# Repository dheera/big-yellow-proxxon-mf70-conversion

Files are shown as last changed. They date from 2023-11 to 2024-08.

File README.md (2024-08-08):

# Big Yellow Proxxon MF70 CNC conversion

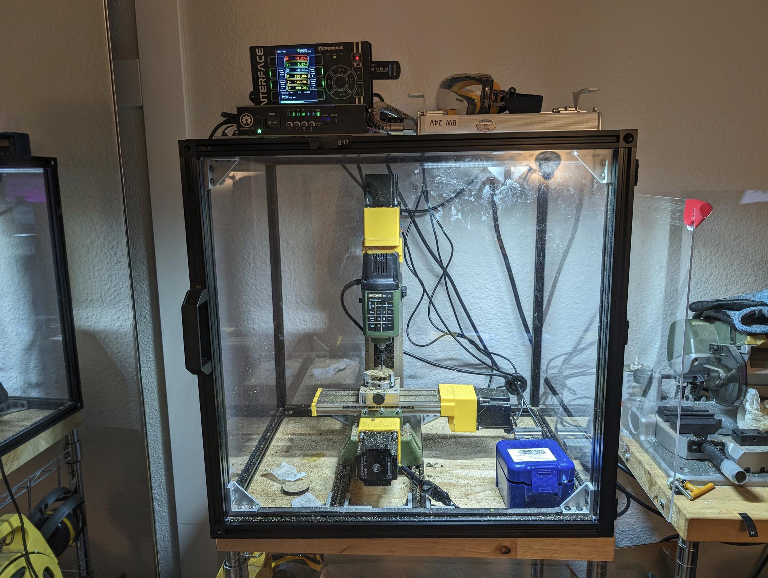
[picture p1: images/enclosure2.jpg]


This repo is a Proxxon MF70 mill CNC conversion based on 3D printed and off-the-shelf mechanical parts, with **Y axis extended from 46mm to 90mm** and **Z axis extended by 15mm**.

I also included a couple parts for if you just want to extend the Y axis for hand milling only, but CNC is the main point of this repo.

I'm lazy to create a name for it, but in the spirit of the [Bubblegum](https://www.youtube.com/playlist?list=PLYxf6JVpXtyO_PyjGGxkbttEl6JiWM5uO) conversion I printed all the parts in yellow so I'm just calling it that.

### What is a Proxxon MF70?

If you are here you probably already have one, but the [Proxxon MF70](https://www.proxxon.com/us/micromot/37110.php) is a cheap, tiny 3-axis mill that sells for around USD 400, sometimes as cheap as 200-300 on Craigslist or eBay and is been a popular target of CNC conversions by hobbyists living in small spaces. The full machine with CNC conversion and enclosure is no larger than a typical 3D printer.

This mill has a number of limitations, but perhaps the biggest of which is that the Y axis is only limited to 46mm of travel. It is fairly straightforward to extend this Y axis to 90mm. The Z axis is also limiting as it only has 70mm of travel, starts from uselessly low, which makes it hard to use a 4th ("A" or rotational) axis. **Both of these limitations are addressed in this conversion.**

There are other limitations with this cheap mill but not addressed here. (Anti-backlash nuts, brushless motor upgrade, new spindle, ACME screws, ball screws, etc. -- but you can still do these things on top of this conversion if you wish.)

If you have a 3D printer to print the parts in this repo, and want a mini **CNC mill for $500-$600 total**, this is it. If you want to spend $1200 or more, there are better options available.

### Why another MF70 conversion?

I wasn't fully happy with any of the existing conversions.

The AliExpress conversion kits are cheap but don't address Y axis or Z axis limitations, use self-tapping screws to hold the entire weight of stepper motors which I am not confident about, and use only 2 out of the 4 mounting screws to hold NEMA23 motors, which is not good for stability. I do, however, like their couplers that attach to the existing handles of the MF70 and use those couplers in this conversion.

The Robotpark conversion has the same issues as the AliExpress kit at a 5X-10X markup, and judging from pictures, seems to just use the same parts as the AliExpress kits.

Proxxon's own CNC-ready MF70 allows a greater Y axis travel of 70mm, which is better than the 46mm, but I am achieving 90mm here. It also does not address the Z axis height at all.

The [Bubblegum](https://www.youtube.com/playlist?list=PLYxf6JVpXtyO_PyjGGxkbttEl6JiWM5uO) conversion is a nicely designed kit but addresses neither Y nor Z axis limitations. I take a couple inspirations from it.

[This](http://www.jarkman.co.uk/catalog/cnc/mf70.htm) conversion involves taking off the knobs fully and purchasing additional shaft couplers, which I also didn't want to do, though if you'd like to do that, you can still use the mounting parts in this repo, and might just need to adjust the M5 spacer lengths.

[This](https://www.thingiverse.com/thing:4375769) conversion is a lot of work and addresses backlash but does not solve the Y or Z axis limitations.

There are a number of other complicated DIY conversions out there that do address the Y and Z axis limitations, but I wasn't happy with any of their designs or complexity. Some involve 5 billion parts, some involve machining metal parts (which is great *after* you have a CNC mill but not before), [some people](https://www.youtube.com/watch?v=0PCznyqI1Co) have effectively replaced the entire machine, which is impressive and I have a lot of respect for, but it is too much for me (If I wanted to do that I might as well build the machine from scratch).

I wanted this to extend the Y and Z axis and stick to 3D printed parts and off-the-shelf parts while keeping the cost of conversion well under the cost of the mill itself.

## Tools
* 3D printer and PETG, ABS, nylon, or other strong and chemically-resistant filament (do not use PLA!)
* Drill press
* Normal 3mm drill bit
* Extra long (120mm long) 3mm drill bit
* 90-degree countersink bit
* Dremel with cutting disc, or other tool that can cut threaded rods
* Blue Loctite

## Off-the-shelf parts

I include McMaster links for all the parts below for convenience, if you want to order them all in one go, and to serve as permalinks for what the exact part should look like. However, McMaster is expensive. If you want to save money you can find equivalent parts for almost everything on Amazon or eBay, though since the suppliers are constantly changing, there is no way to permalink to those sites. I have included Amazon search result links below, so verify that they match the specified dimensions before purchasing.

* 4 x M3 threaded rod, 2 cut to ? for X axis and 2 cut to ? for Y axis [McMaster](https://www.mcmaster.com/90024A218/) | [Amazon](https://www.amazon.com/s?k=m3+threaded+rod+300mm)
* 6 x M3 square nut, 5.5mm x 5.5mm x 1.8mm [McMaster](https://www.mcmaster.com/97258A101/) | [Amazon](https://www.amazon.com/s?k=m3+square+nut+1.8mm)
* 6 x ID=6 OD=12 L=4.5 thrust ball bearings [McMaster](https://www.mcmaster.com/7806K58/) | [Amazon](https://www.amazon.com/s?k=6x12x4.5+ball+bearing)
* 1 x ID=6 OD=13 L=5 steel spacer [McMaster](https://www.mcmaster.com/92871A241/) 
* 1 x ID=6 OD=13 L=2 steel spacer [McMaster](https://www.mcmaster.com/92871A198/)
* 8 x ID=5 OD=10 L=35 aluminum spacer [McMaster](https://www.mcmaster.com/94669A148/)
* 4 x ID=5 OD=10 L=45 aluminum spacer [McMaster](https://www.mcmaster.com/94669A152/)
* 4 x M5 L=50 flat head countersunk screws [McMaster](https://www.mcmaster.com/92125A228/)
* 4 x M5 L=65 flat head countersunk screws [McMaster](https://www.mcmaster.com/92125A230/)
* 4 x M5 L=75 flat head countersunk screws [McMaster](https://www.mcmaster.com/92125A109/) -- if you want to save money you can also just get a box of L=75 and skip the L=50 and L=65 above, but you'll have a hell of a time tightening lock nuts over the extra length
* 4 x M3 L=50 hex bolt socket cap screws
* AliExpress MF70 NEMA23 conversion shaft couplers -- you only need the "round parts" from the conversion kit -- there are some sellers which will sell only those parts to you [AliExpress](https://www.aliexpress.us/w/wholesale-mf70-nema23.html?spm=a2g0o.productlist.search.0)
* 3 x good quality NEMA23 motors with 5mm mounting holes (some have 4mm holes, but this kit is designed for 5mm) [OpenBuilds](https://openbuildspartstore.com/nema-23-stepper-motor/) | [StepperOnline](https://www.omc-stepperonline.com/p-series-nema-23-bipolar-1-8deg-1-26nm-178-4oz-in-2-8a-2-5v-57x57x56mm-4-wires-23hp22-2804s) 

### 3D printed parts

For the CNC conversion, print all the parts starting with **all-** and **cnc-** in the **stl/** directory.

If you just want a hand mill with Y axis extension, print everything starting with **all-** and **hand-** and ignore the CNC parts. You also only need a fraction of the off-the-shelf parts above, I'm sure you can figure it out.

I recommend printing everything at 100% infill with PETG, ABS, nylon, or other good material. I highly recommend you do not use PLA. Don't skimp on the infill, this is a mill, and if you're using PETG it will cost you a whopping $9 to print all these parts at 100%.

I recommend printing parts with large surface area (all-y-channel, cnc-x-rightplate, cnc-y-frontplate, cnc-z-topplate) with a brim to avoid lifting and warping at the corners, as the **flatness of the bottom surface is crucial** on many parts. If you don't have lifting/warping problems you can ignore this. Besides using a brim, for PETG, 2 things help to avoid warping: (a) use a higher bed temp like 90 C (b) use an enclosure or put your 3D printer in a closet so the ambient temperature rises to around 30 C - 40 C.

### Extra hardware

## Instructions

### Take apart the X and Y axes

Remove the 2 axis stage, take apart the Y axis (noting that the lead screw is left-threaded), and then take apart the X axis (right-threaded) until you are down to this. Note that the "Proxxon" logo is on the front side, but we will take that off later, so you may want to mark the front side of the aluminum plate with a grease pen or scribe. Note that Proxxon's X and Y axis aluminum plates are intentionally NOT perfectly symmetrical by design, so when you put them back together the direction matters or you will not be able to assemble it.

Drop in the 3D printed "all-y-channel". It should fit snugly. Note that the channel is not symmetrical and there is a correct front and back side. You may want to mark the front end of this as well for convenience. You may have to slightly loosen the screws slightly to drop the channel in. Don't take them off fully yet, to ensure the holes you drill in the next step are properly aligned.

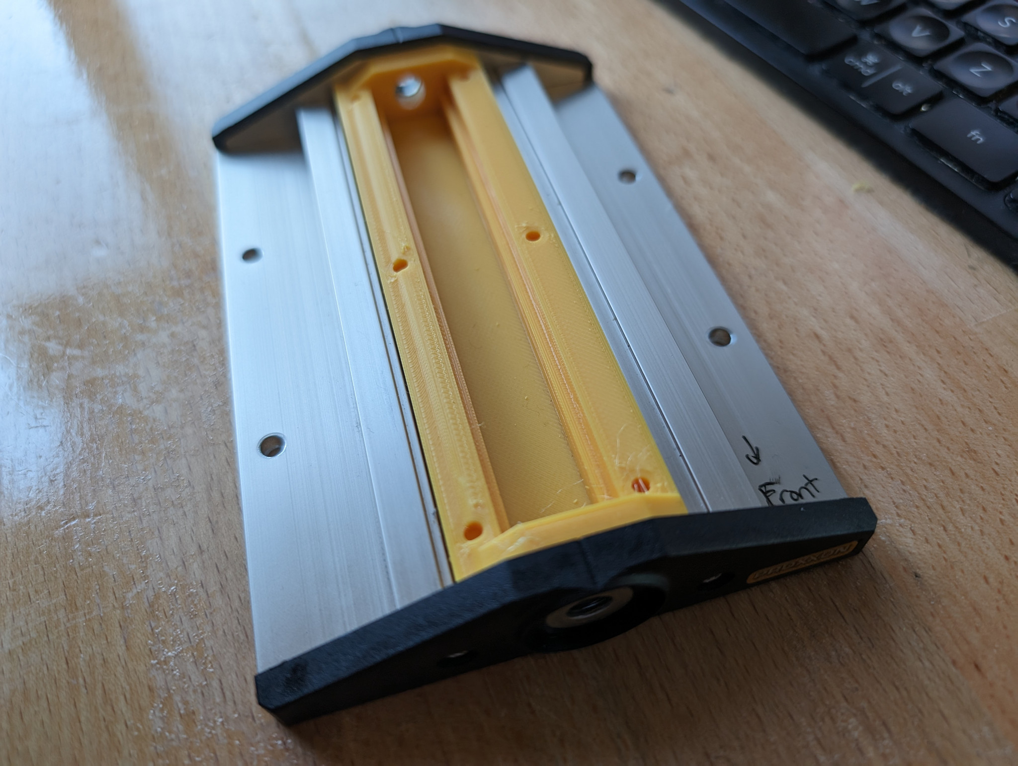
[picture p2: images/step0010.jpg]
step0010


### Modify the Y axis plate

With a drill press and regular 3mm drill bit, drill out the 6 marked holes in the 3D printed channel all the way down and drill fully through the aluminum plate below. You can also, if you prefer, just barely touch the aluminum to mark the center, remove the channel, and then drill out the aluminum, to avoid aluminum chips accumulating inside the square nut inserts.

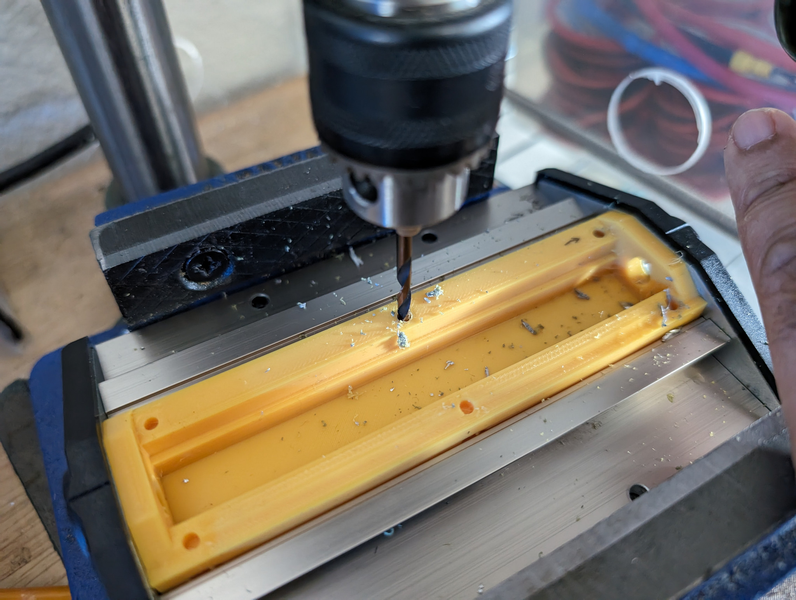
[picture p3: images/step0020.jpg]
step0020


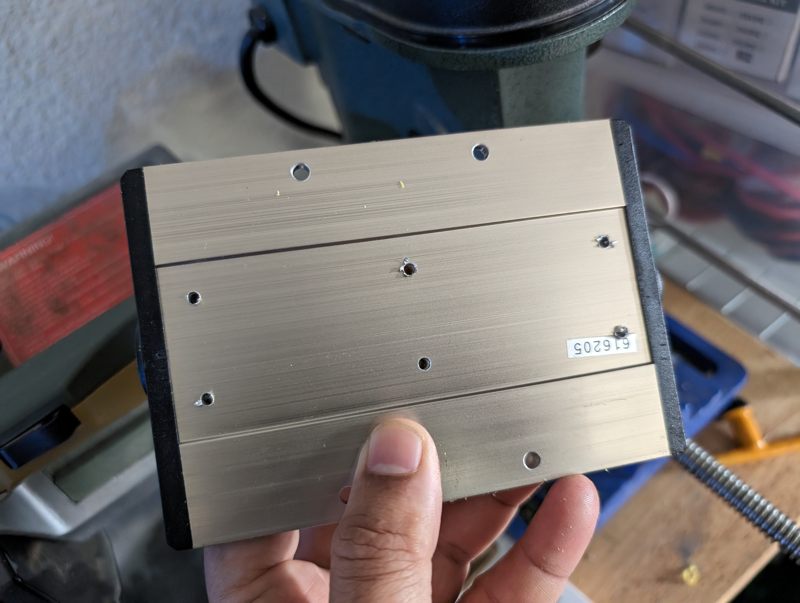
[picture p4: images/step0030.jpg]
step0030


Remove the manufacturer-supplied end pieces of the Y axis. These will not be needed anymore. Countersink the holes from the back of the aluminum plate with a 90 degree countersink bit and verify countersunk screws sit flush.

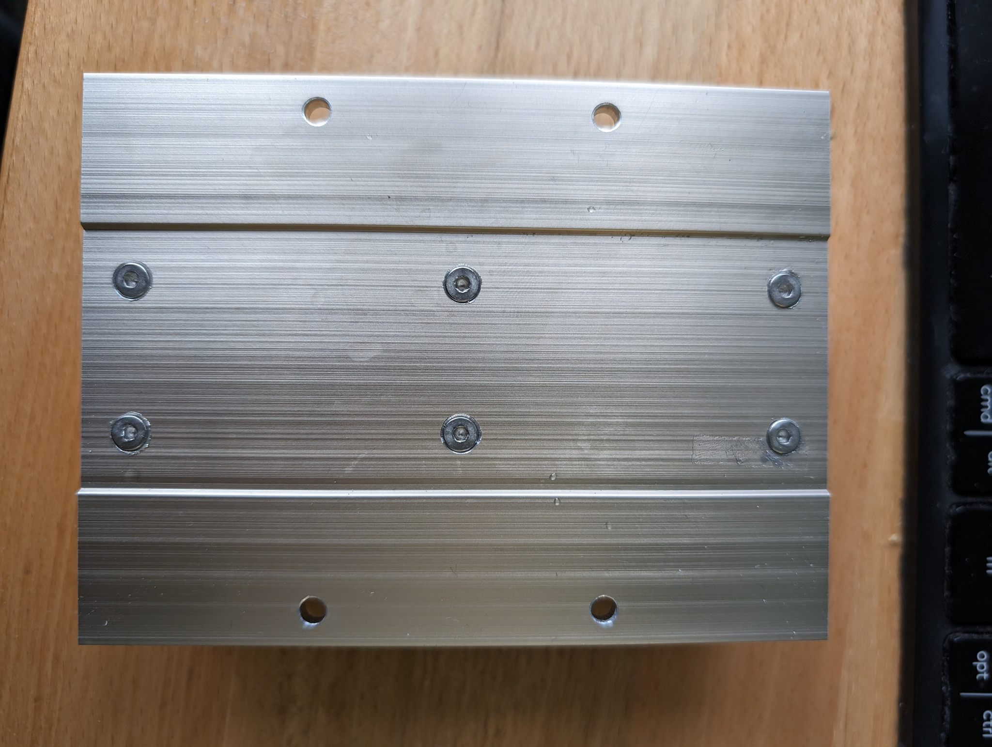
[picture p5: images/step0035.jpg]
step0035


Remove "all-y-channel", make sure the 6 slots on the side are clear of chips, and insert the 6 square threaded M3 nuts from the side.

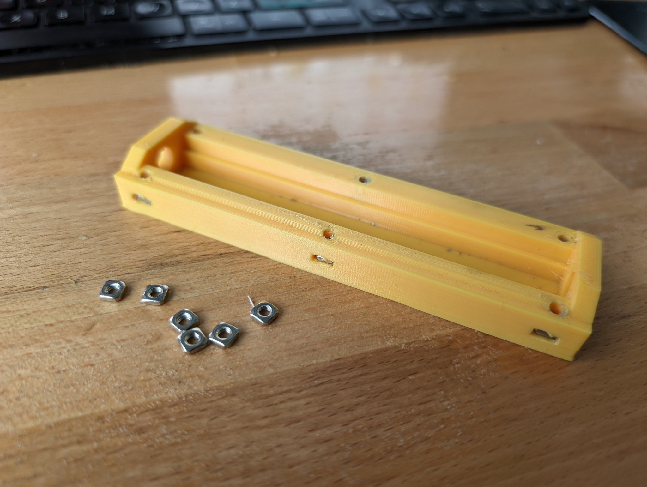
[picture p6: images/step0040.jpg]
step0040


Slide into the aluminum plate together with the carriage, brass spacer that goes with the carriage, and delrin nut, and use countersunk M3 screws to fix the 3D printed channel in place. With the Delrin nut in place, the carriage should be constrained by the ends of the 3D printed channel, and should slide smoothly from end to end. Make sure it does not have any resistance at the metal-plastic boundaries. If it does, your 3D printer may not be dimensionally accurate and you may have to do some sanding.

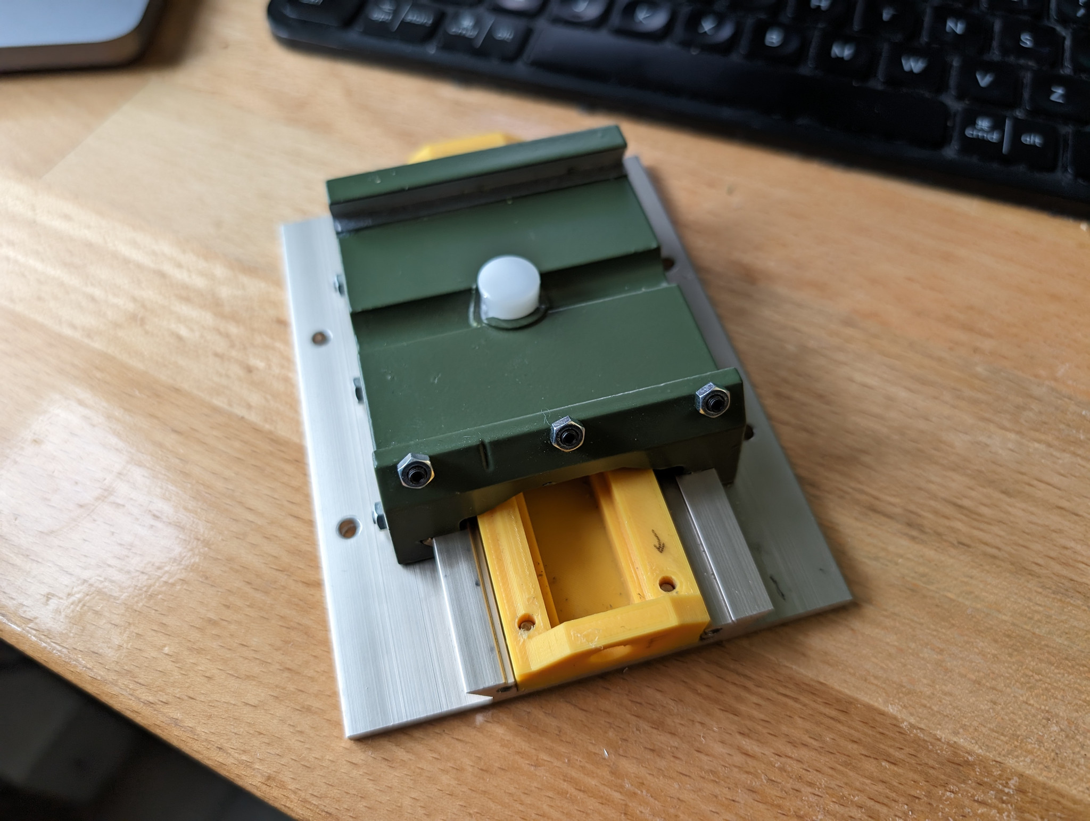
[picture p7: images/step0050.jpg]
step0050


Use the 120mm extra-long M3 drill bit to carefully drill out the 2.5mm channels to 3mm. Use plenty of machining oil and go slowly to avoid breaking the bit. (We will no longer use the self-tapping screws and instead put M3 threaded rods though these channels which will hold things much more securely.) Work the drill from both sides to get all the way through the channel. Unfortunately I did not take a picture of this step for the Y axis, so here is a picture of the same procedure on the X axis for reference, but do this for the Y axis:

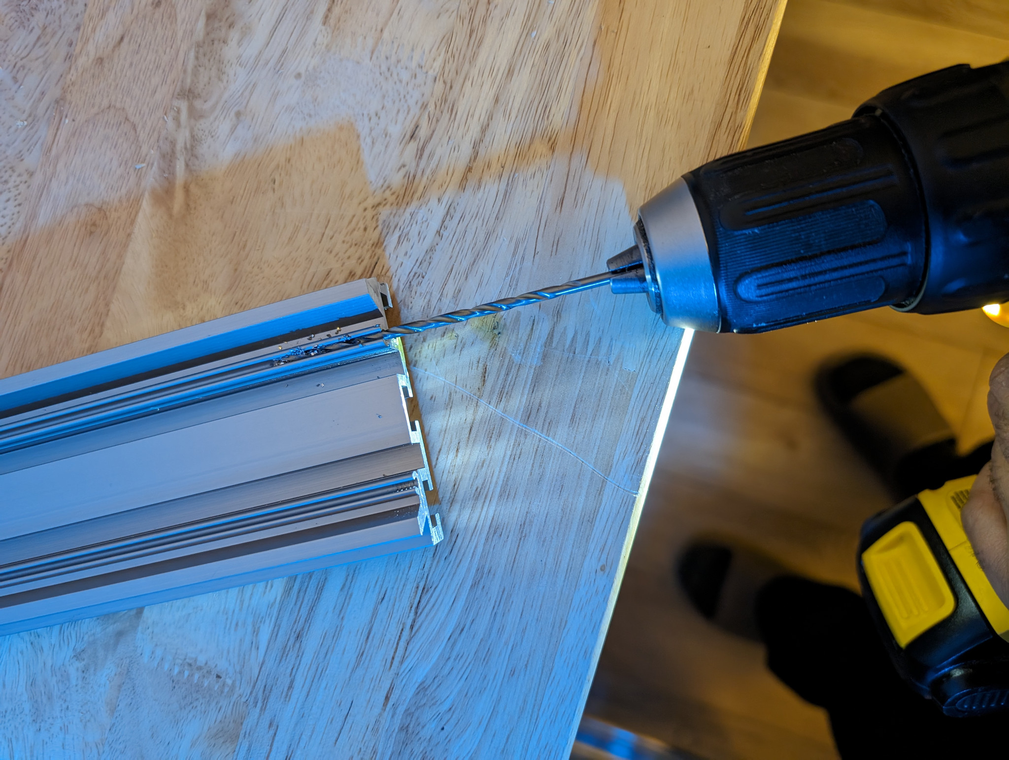
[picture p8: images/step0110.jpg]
step0110


### Reassemble the Y axis

Install all-y-backplate on the back side. Install cnc-y-frontplate on the front side. Cut two M3 threaded rods to appropriate length with a Dremel. Use them along with washers and M3 locknuts on both sides to tighten them all in place. Make sure the rods do not protrude beyond the locknut on the front side.

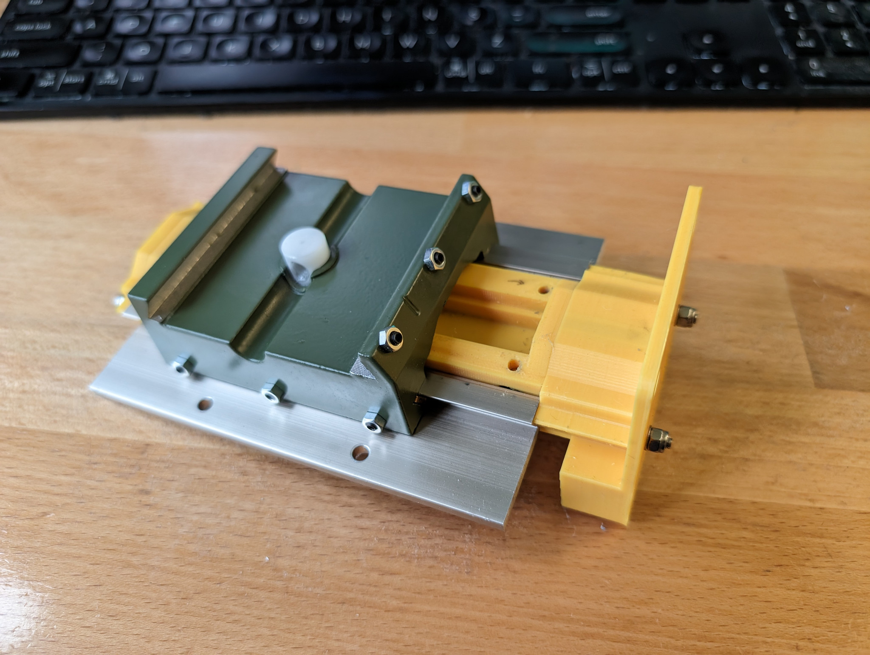
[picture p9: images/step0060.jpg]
step0060


Make sure the big green thing is able to move freely beyond the end of the aluminum plate without hitting any resistance over the plastic region. If there is friction you may have dimensional issues with your print.

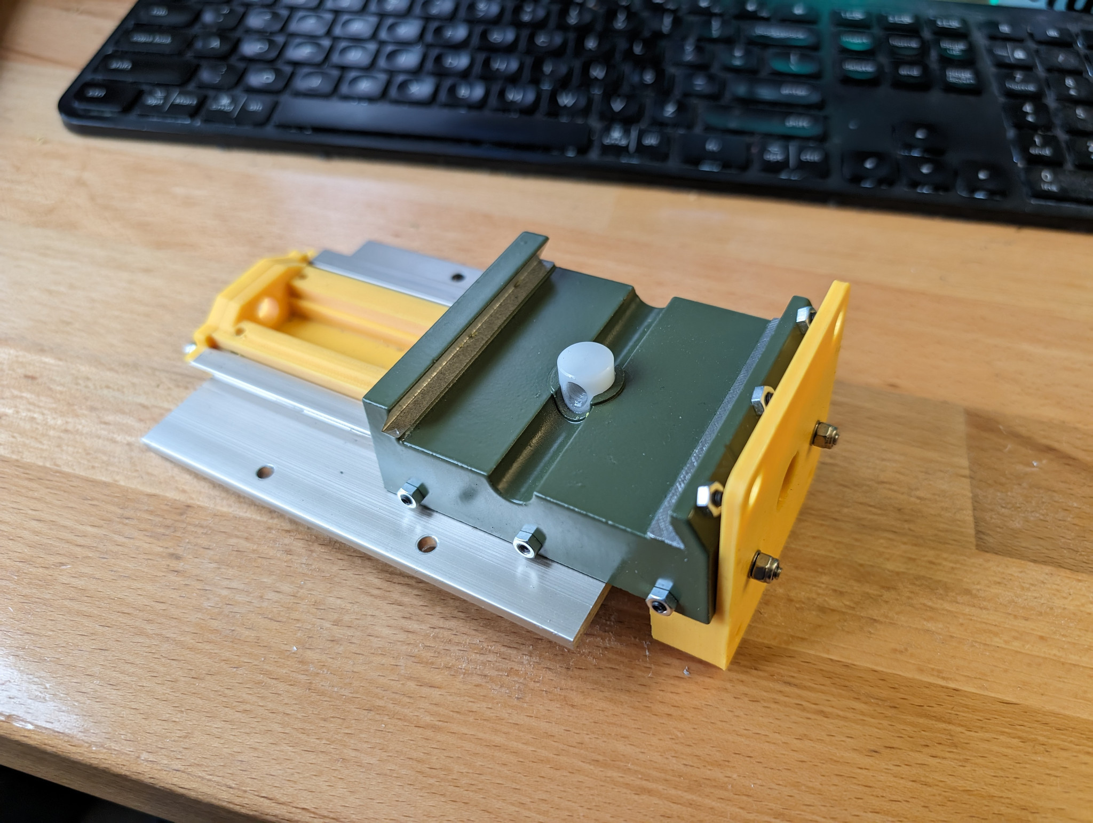
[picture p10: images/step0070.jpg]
step0070


Install the Y axis shaft. On the front side there should be a ball bearing (which comes as a hamburger of 3 components) and a 5mm spacer, and the AliExpress coupler should be installed as shown. On the back side there should be a ball bearing and the (left-threaded) locknut. You will need blue Loctite even though it is a nylon locknut because there will not be enough thread to engage the nylon anymore after this modification.

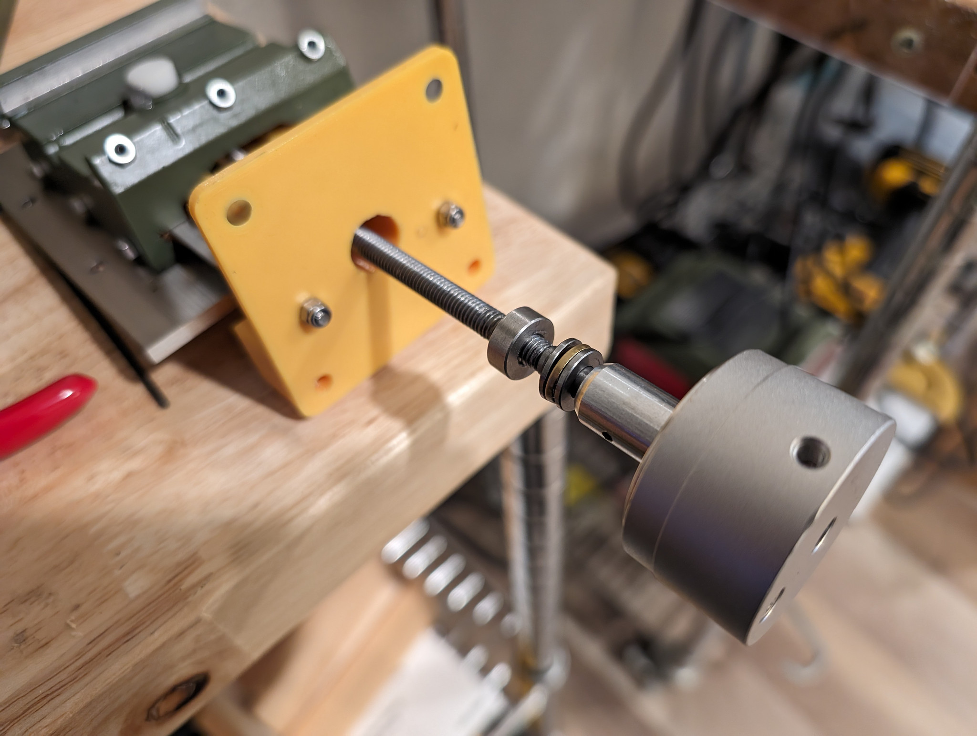
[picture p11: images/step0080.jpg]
step0080


Put the M5 countersunk screws in and entire Y axis back on the mill. Make sure to push the bottom against the cast iron before tightening so it is properly supported.

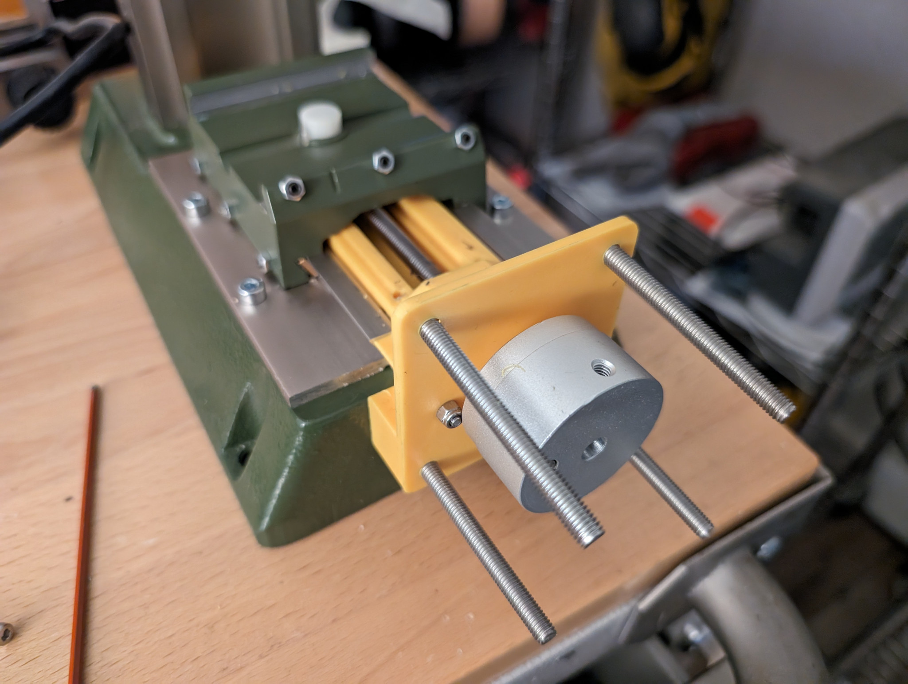
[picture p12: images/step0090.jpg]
step0090


Install the stepper motor. Use **cnc-stepper-nut-tool** to help you, the lock nuts can be annoying.

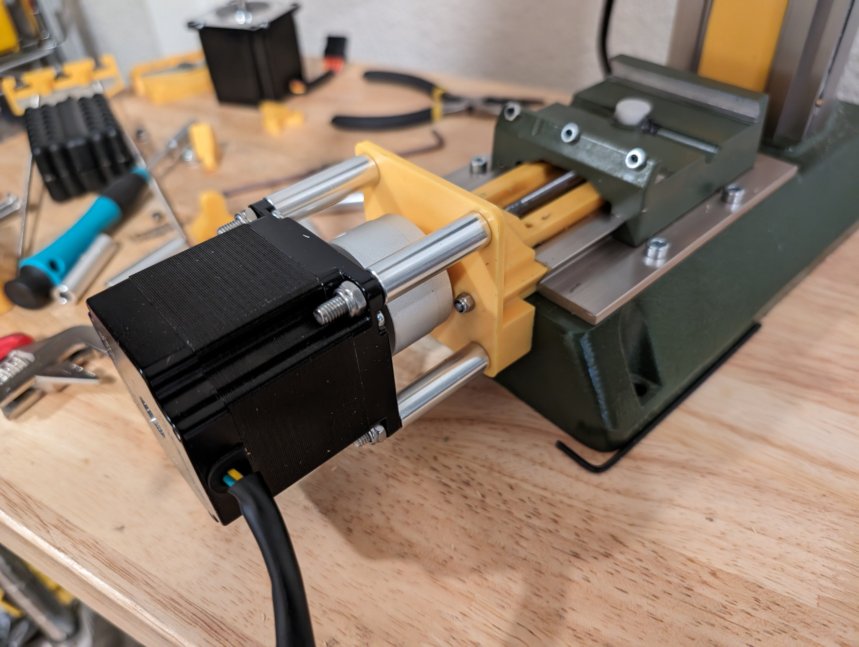
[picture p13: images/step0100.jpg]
step0100


### Modify the X axis plate

Use the 120mm extra-long M3 drill bit to carefully drill out the 2.5mm channels to 3mm. Use plenty of machining oil and go slowly to avoid breaking the bit. (We will no longer use the self-tapping screws and instead put M3 threaded rods though these channels which will hold things much more securely.) Work the drill from both sides to get all the way through the channel.

step0110

### Reassemble the X axis

Insert the original manufacturer's metal plates into the X axis parts. (I know, this is different from the Y axis; on the Y axis we discarded these plates but on the X axis we are going to use them.)

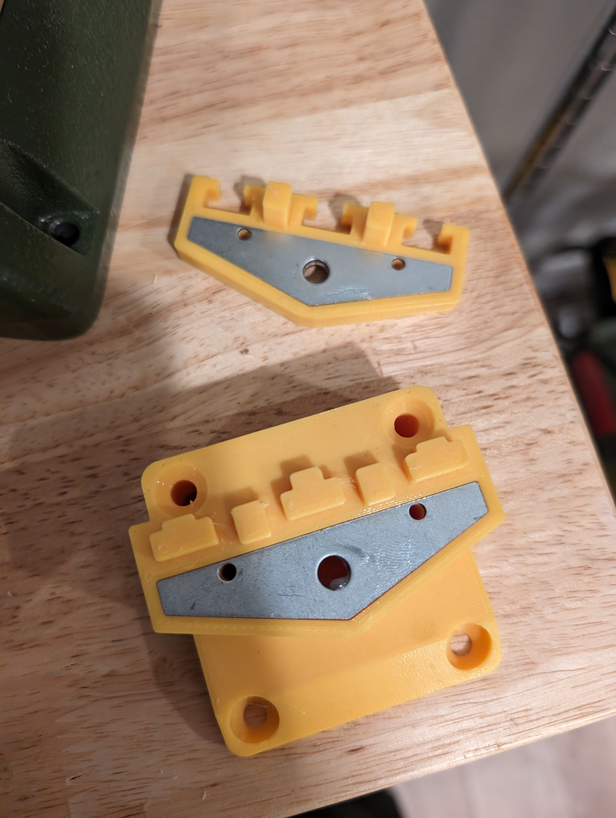
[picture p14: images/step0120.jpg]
step0120


Fix them in place with two M3 threaded rods cut to length.

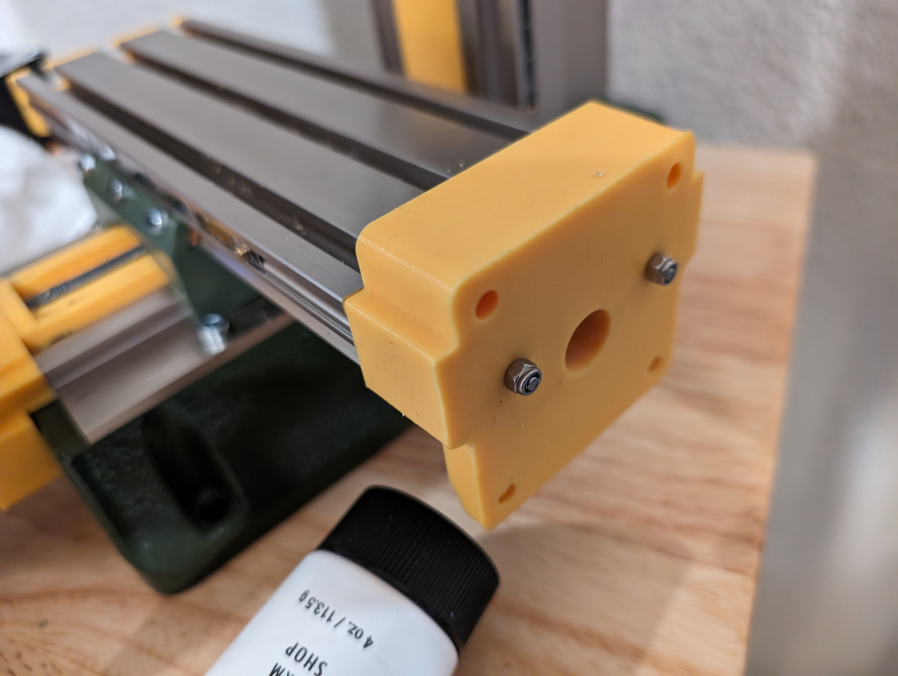
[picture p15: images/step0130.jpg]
step0130


Install the lead screw. On the right side you have a 2mm spacer (I use 2 washers here, but avoid the practice of stacking washers if you can), a hamburger roller bearing, and the AliExrpess shaft coupler installed. On the left you have a hamburger roller bearing and the lock nut. Again you need Loctite because the screw threads will not be enough to engage the nylon.

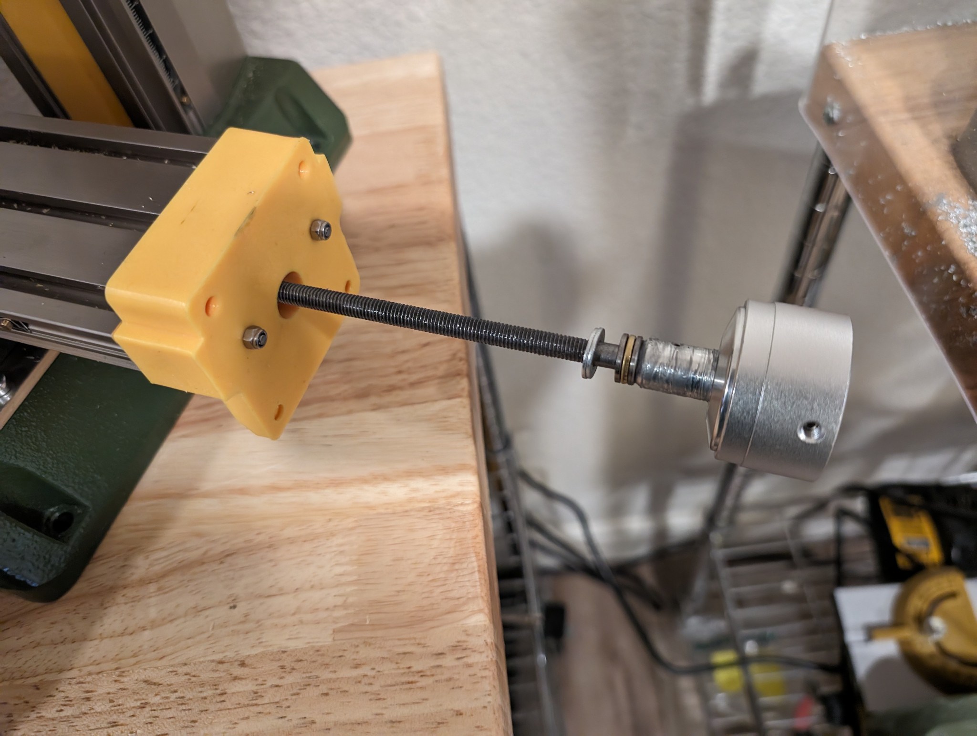
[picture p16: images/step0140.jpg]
step0140


Install the stepper motor. Use **cnc-stepper-nut-tool** to help you, the lock nuts can be annoying.

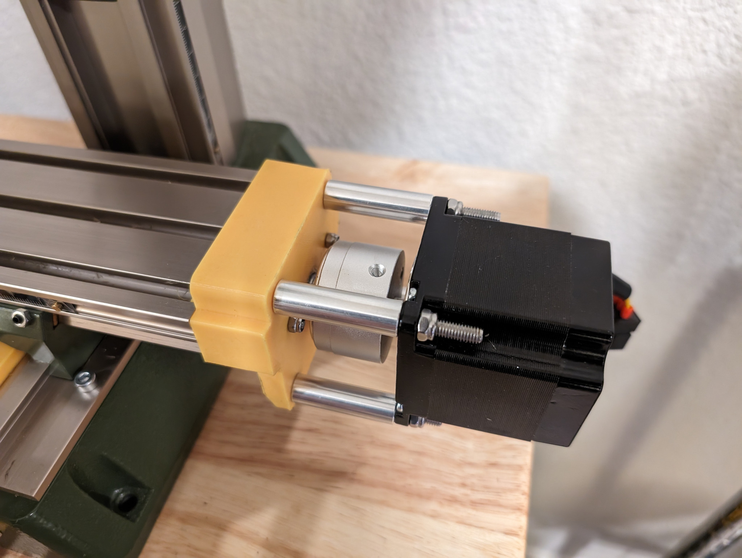
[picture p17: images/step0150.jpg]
step0150


### Take apart the Z axis

Remove thick plastic cover at base of the mill, which will give us additional clearance to the back of the mill.

Remove the 4 M3 screws on top of the Z axis. CAREFULLY turn until the cap and lead screw comes loose from the milling head, taking care not to drop the milling head.

Proceed to remove the locknut that holds the Z axis lead screw in place. Use **cnc-z-nut-tool** to help you remove the lock nut that holds the Z axis lead screw in place.

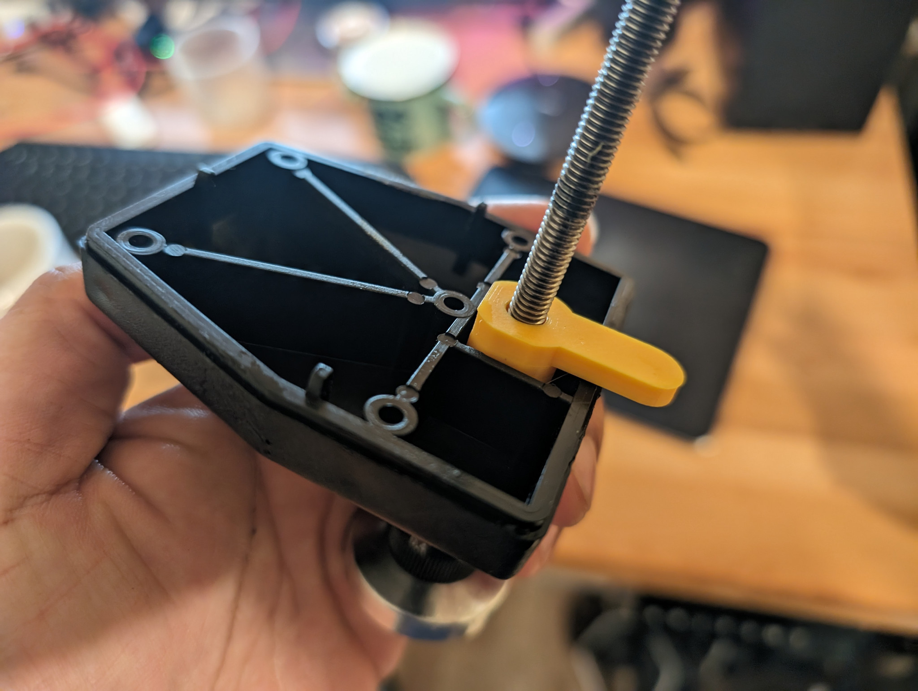
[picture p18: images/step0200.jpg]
step0200


### Reassemble the Z axis

Now reassemble the Z axis, using both parts A and B, and using two ball bearings, one on each side of the 3D printed parts.

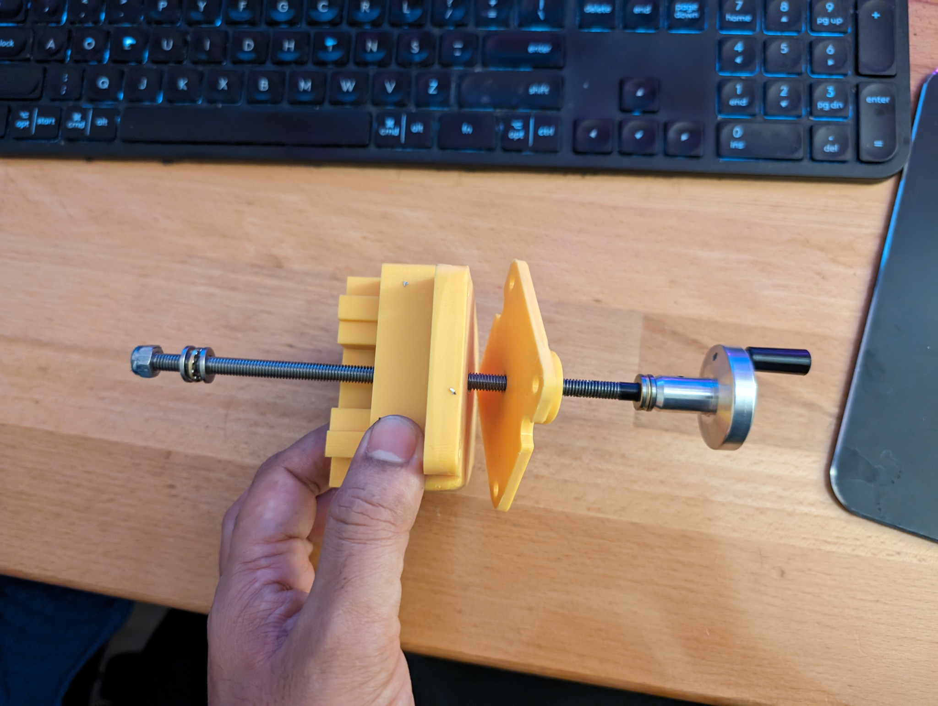
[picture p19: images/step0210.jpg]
step0210


Secure the lock nut in place. Tighten until there is no backlash but do not over-tighten. Again you can use the same **cnc-z-nut-tool** to help you.

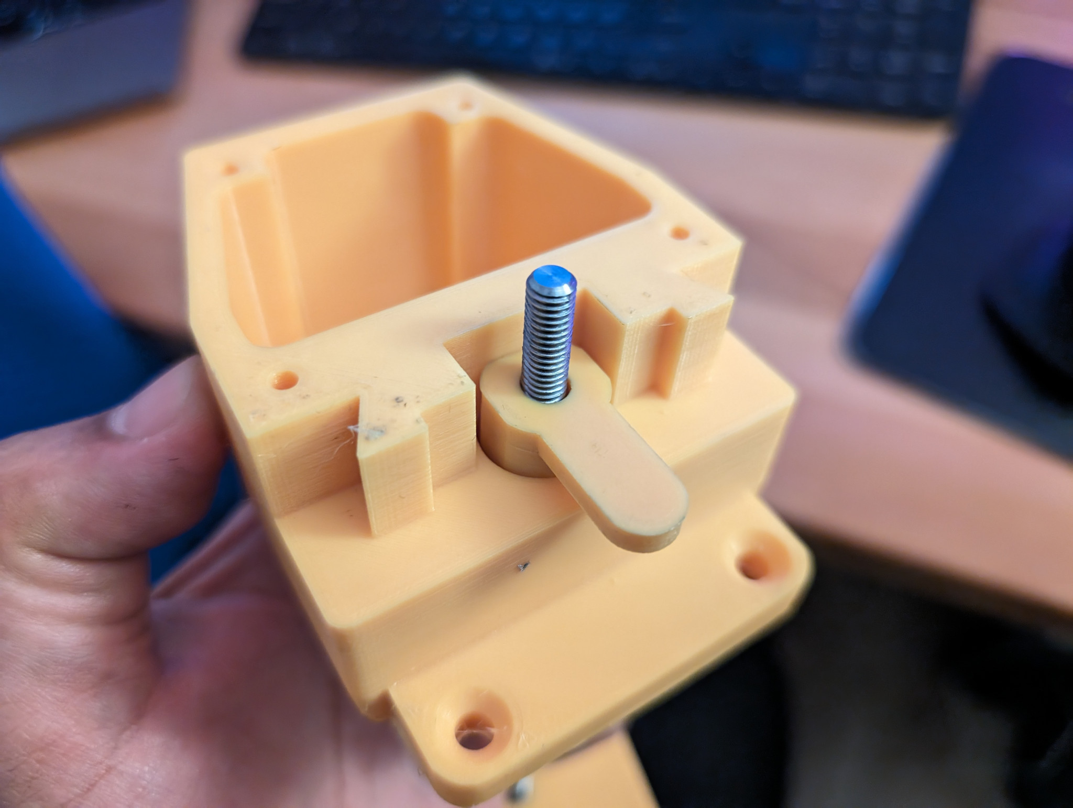
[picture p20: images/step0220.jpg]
step0220


Install the AliExpress shaft coupler and stepper motor as usual.

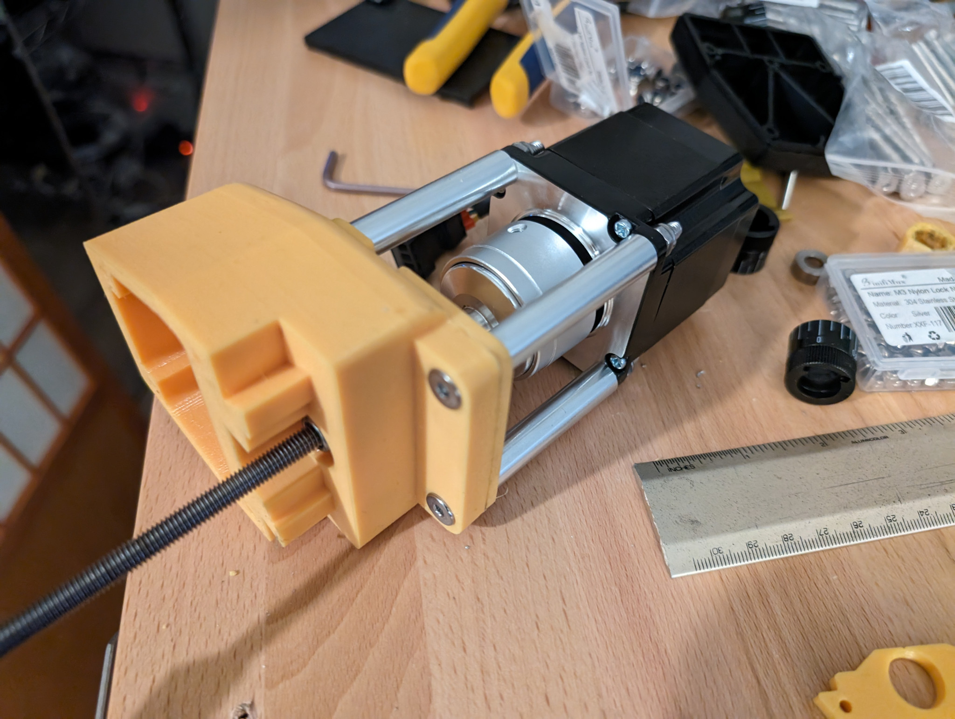
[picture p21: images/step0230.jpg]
step0230


Install the Z axis back on with the head. Put 4 new M3 50mm long bolts to secure it (the original ones will be too short).

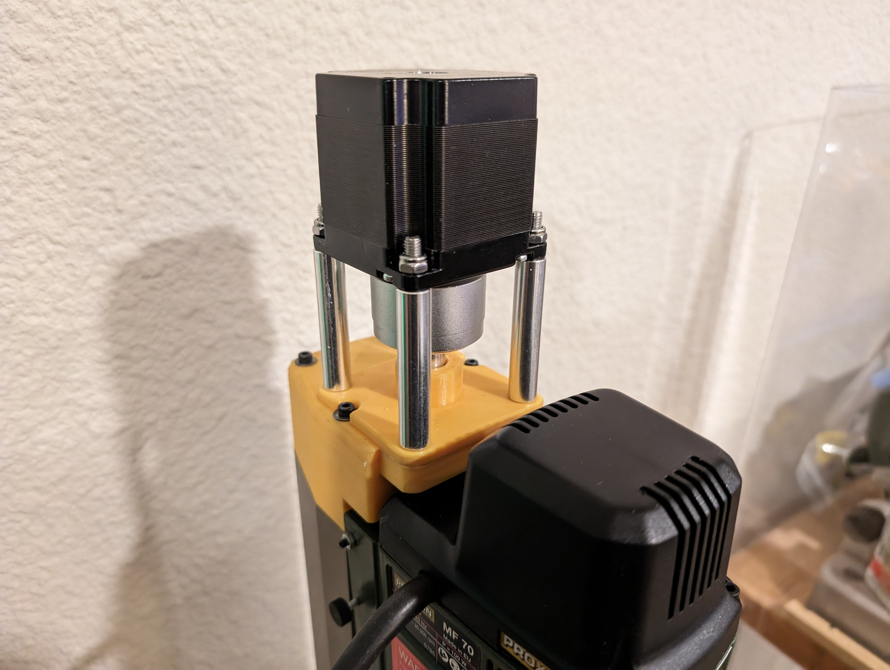
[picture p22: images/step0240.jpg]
step0240


IMPORTANT! Insert this Z axis stop piece into the channel, which will stop the head before it falls out of the Z axis leadscrew. If you wish you can put a dot of adhesive to hold it in place, but it will hold itself behind the black plastic tab just fine.

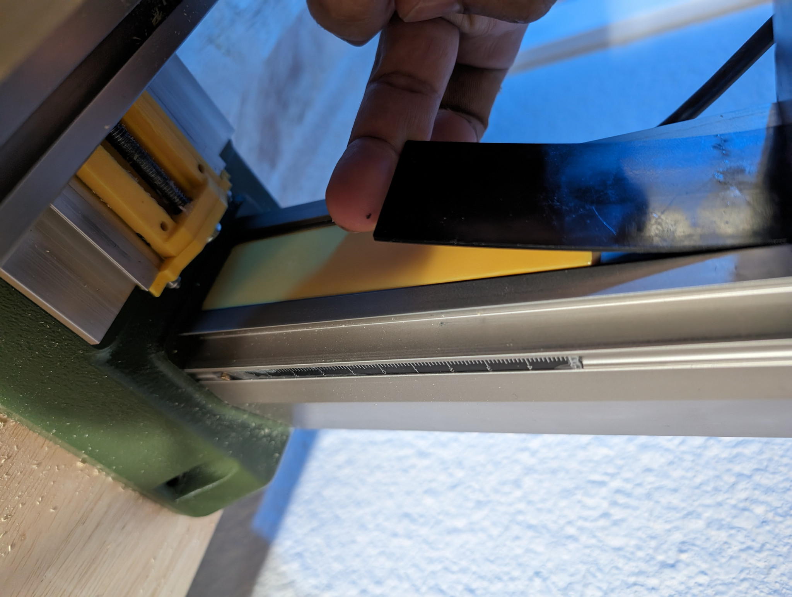
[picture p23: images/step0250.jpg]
step0250


### Final touches

Put the covers over the couplers to help prevent chips landing inside. They should snap in place.

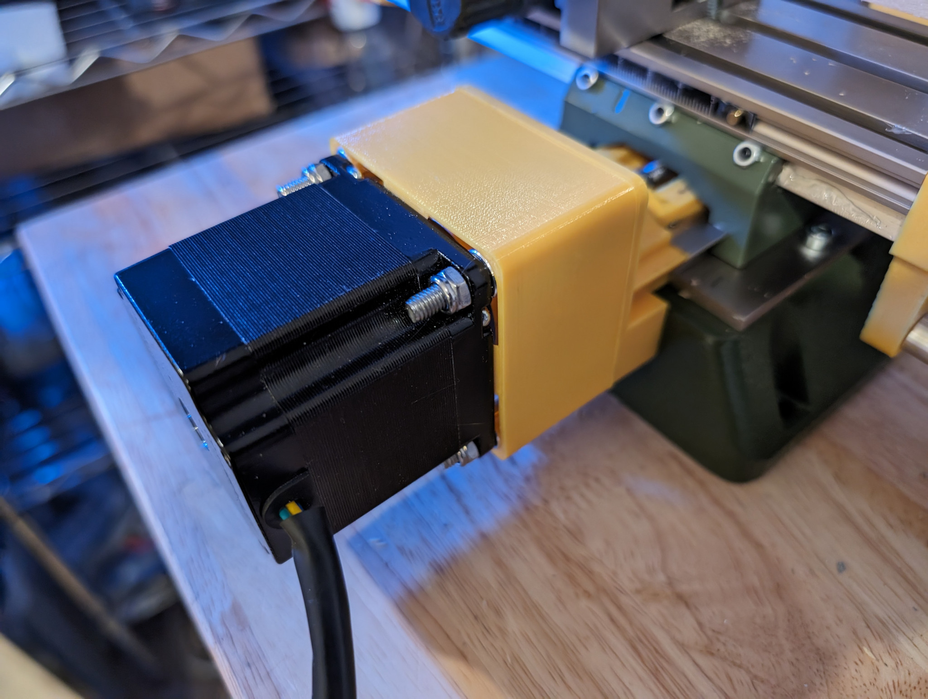
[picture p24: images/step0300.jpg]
step0300


Finished.

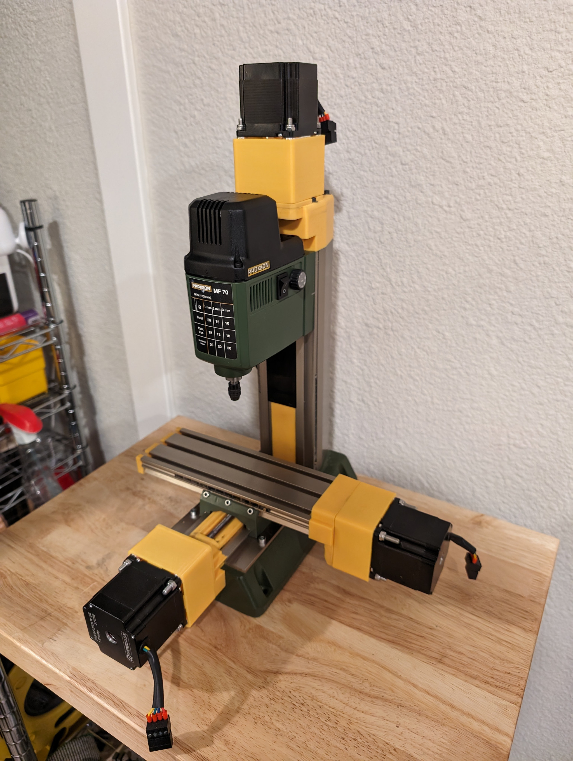
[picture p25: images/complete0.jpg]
complete conversion


You can build an enclosure if you want. I highly recommend it.

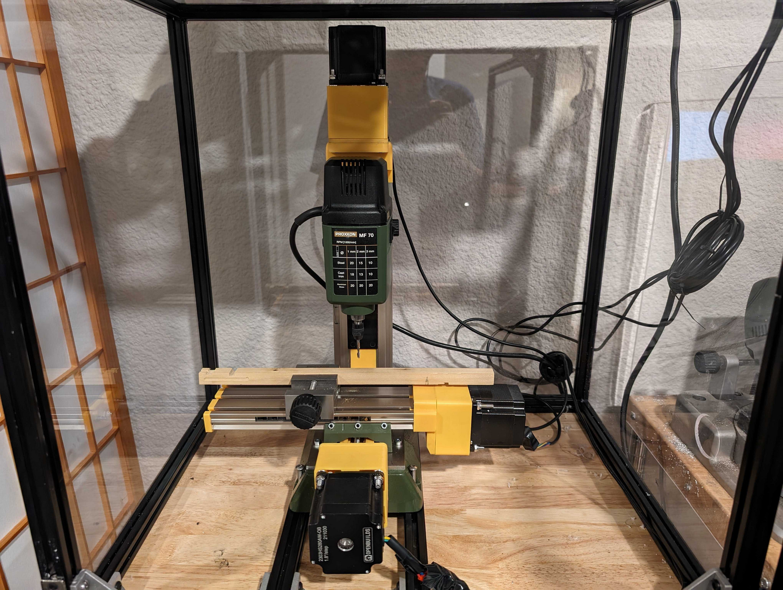
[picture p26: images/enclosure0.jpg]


Great for milling out tiny decorative items out of brass!

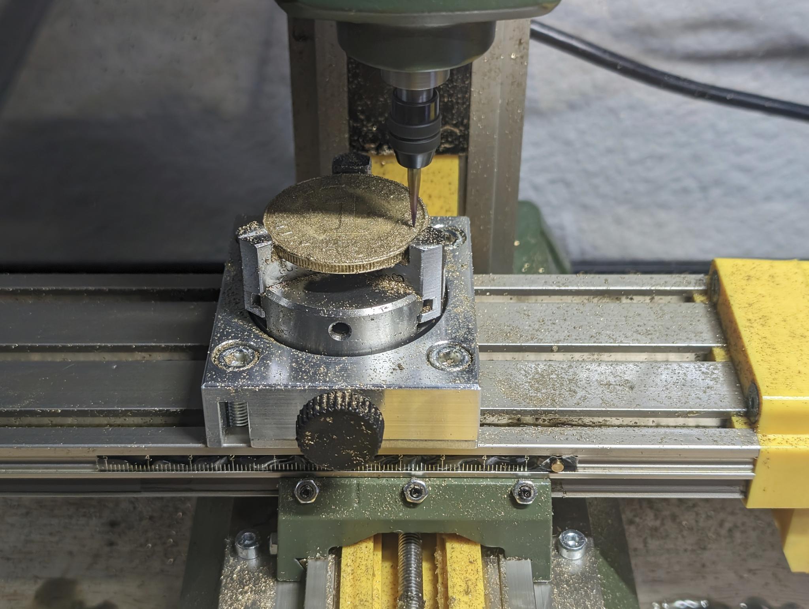
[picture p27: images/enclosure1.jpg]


Example of a finished piece I cut on this mill after tumbling in a vibratory tumbler for a few hours. The bas relief is generated from a picture from my travels with my partner with a custom computer vision pipeline. (We thought this rock formation looked "painted" so we made a huge paintbrush prop for the picture)

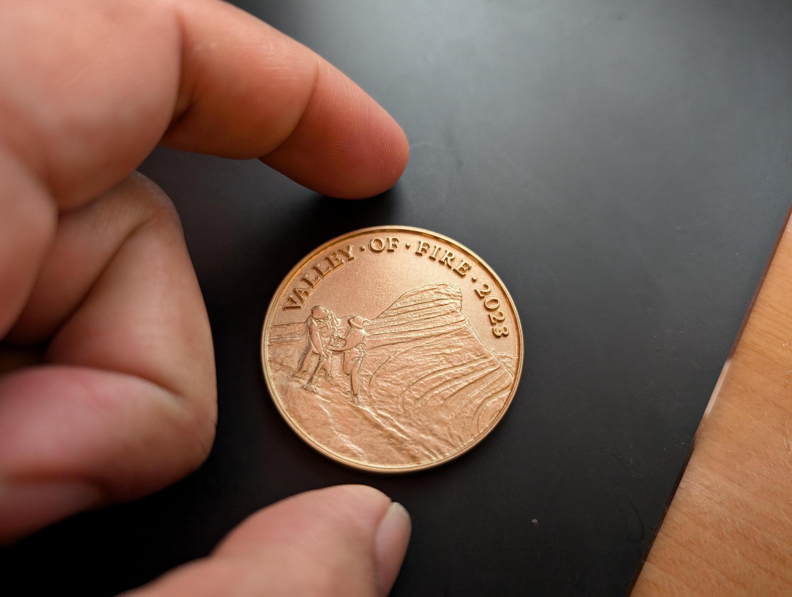
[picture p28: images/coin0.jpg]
coin complete conversion


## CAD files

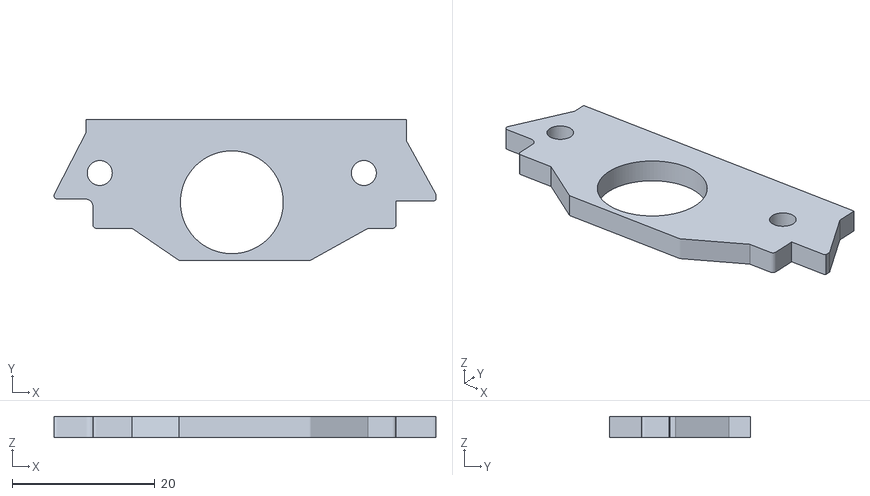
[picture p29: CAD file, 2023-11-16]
src/include/profile_outer.stl
53.5 x 19.8 x 3.00

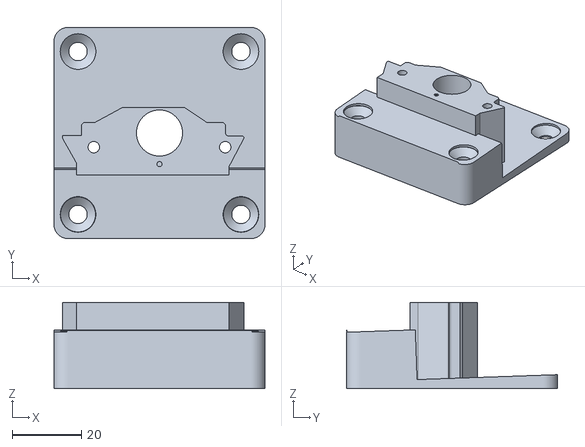
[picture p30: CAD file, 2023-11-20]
stl/cnc-y-frontplate.stl
61.0 x 61.0 x 25.0

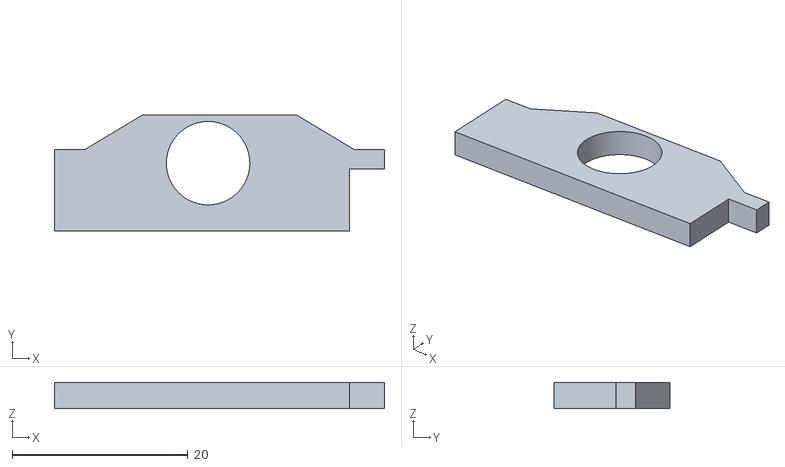
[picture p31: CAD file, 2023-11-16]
src/include/profile_inner.stl
37.6 x 13.2 x 3.00

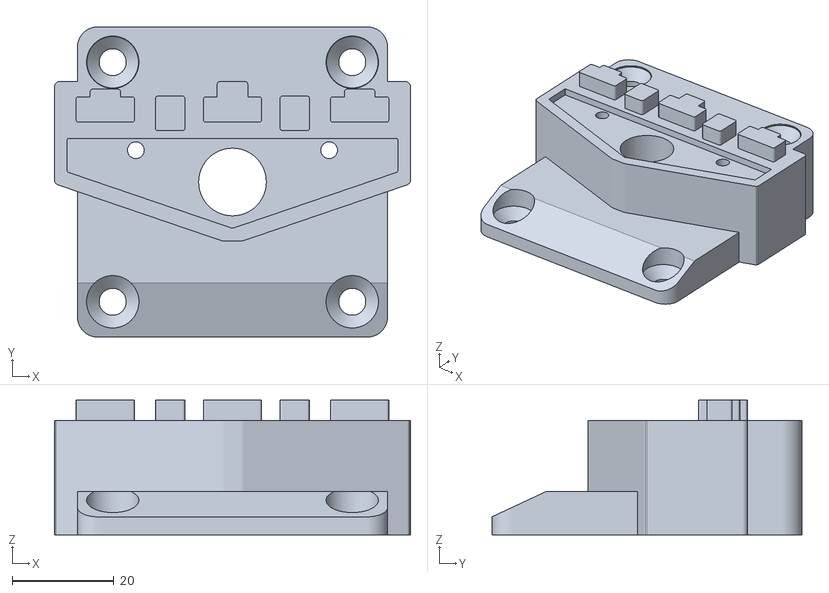
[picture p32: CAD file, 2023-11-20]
stl/cnc-x-rightplate.stl
70.0 x 61.0 x 26.5

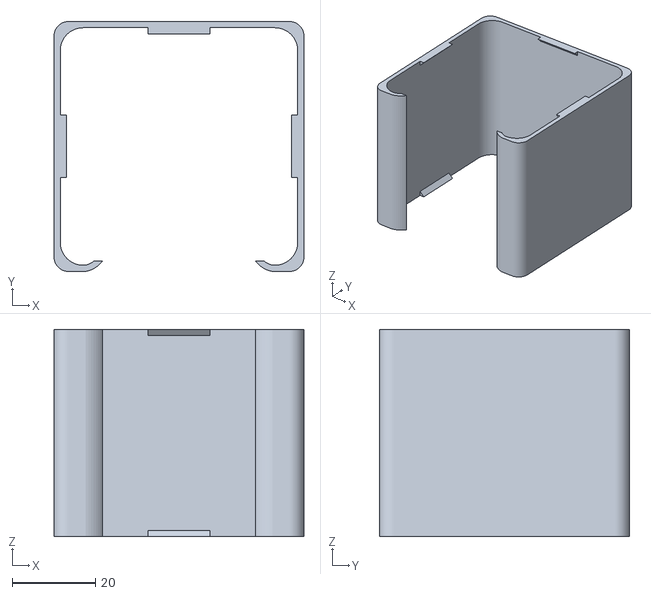
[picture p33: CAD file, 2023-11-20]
stl/cnc-z-cover.stl
60.0 x 60.0 x 49.7

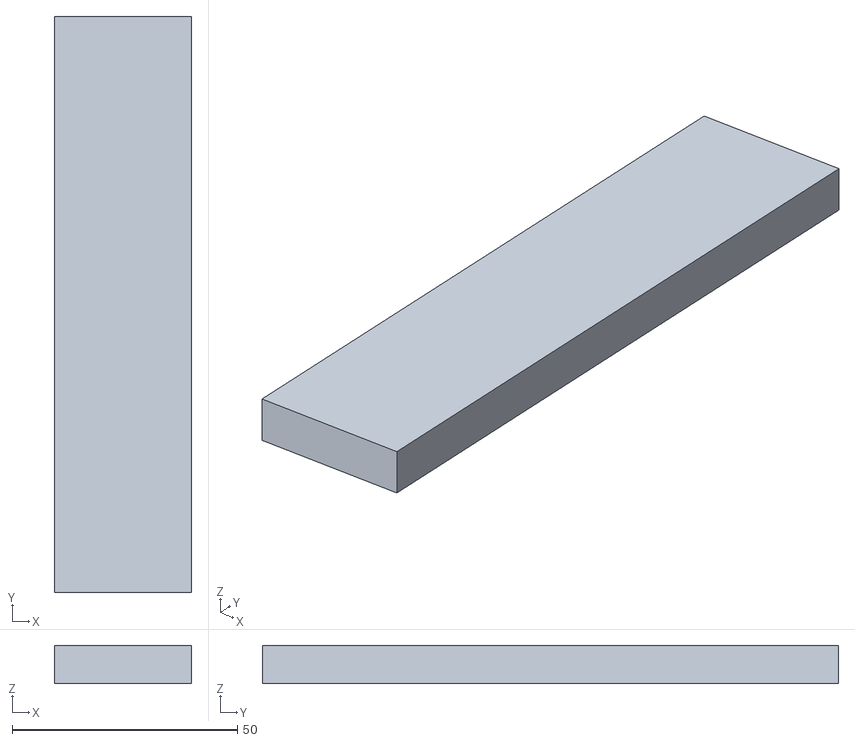
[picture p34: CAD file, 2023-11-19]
stl/cnc-z-stop.stl
30.5 x 128.0 x 8.50

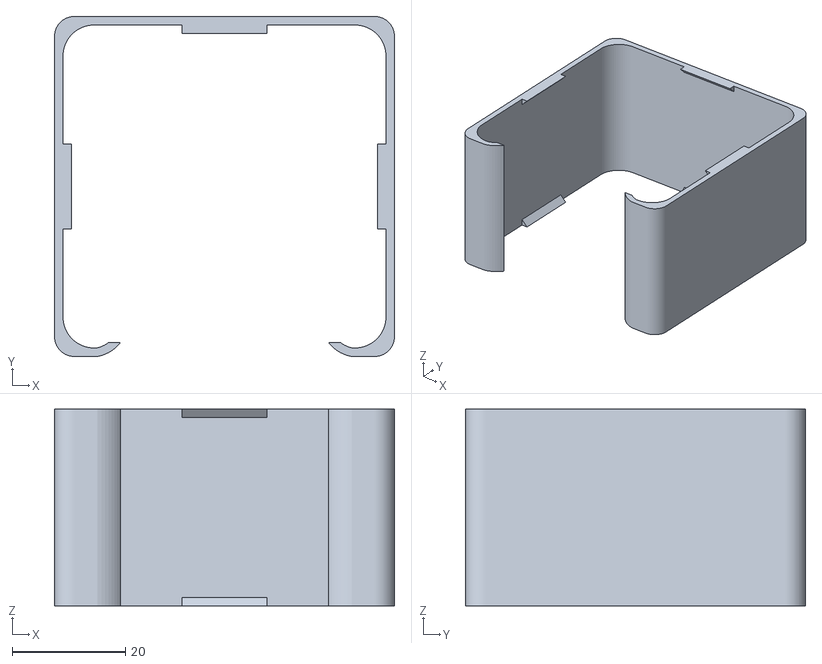
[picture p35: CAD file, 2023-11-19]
stl/cnc-x-cover.stl
60.0 x 60.0 x 34.7

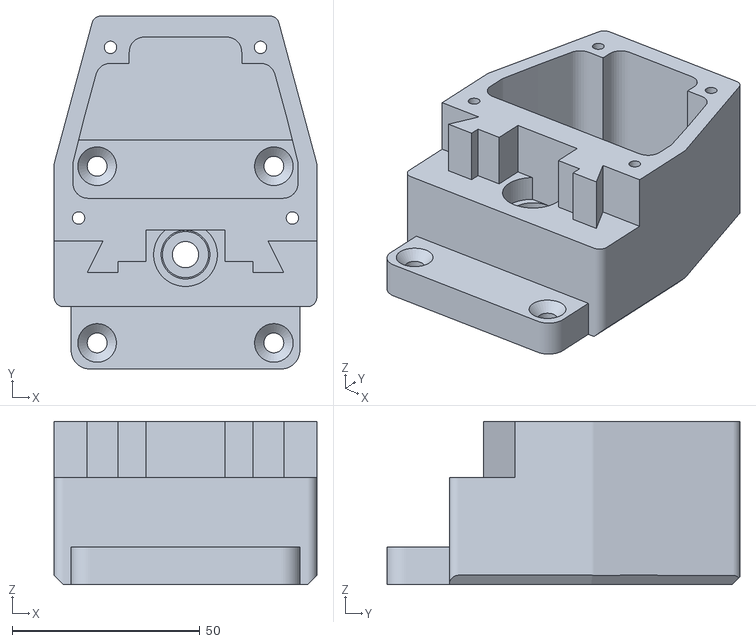
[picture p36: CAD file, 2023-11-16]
stl/cnc-z-topplate-a.stl
70.0 x 94.1 x 43.5

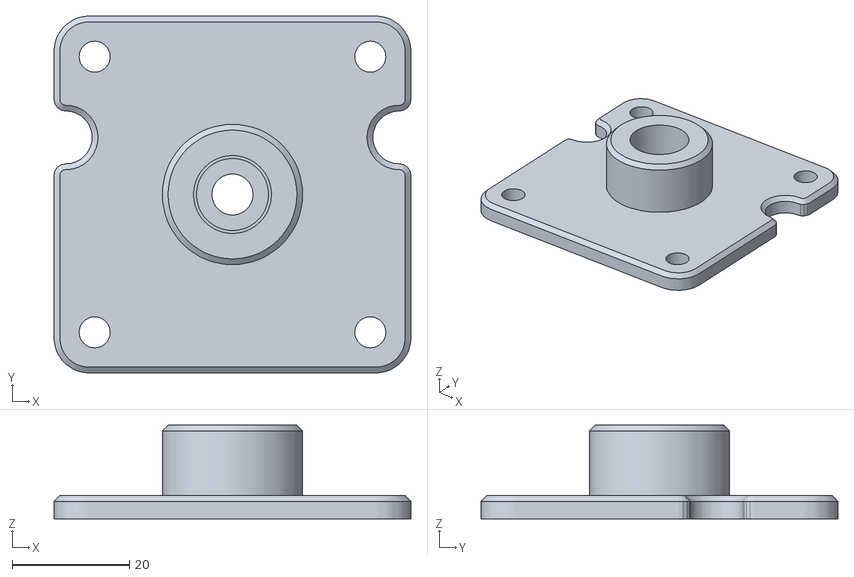
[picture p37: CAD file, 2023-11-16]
stl/cnc-z-topplate-b.stl
61.0 x 61.0 x 16.0

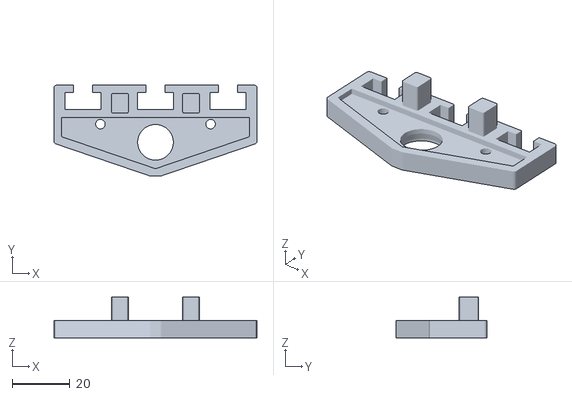
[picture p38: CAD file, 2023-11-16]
stl/cnc-x-leftplate.stl
70.0 x 31.4 x 14.0

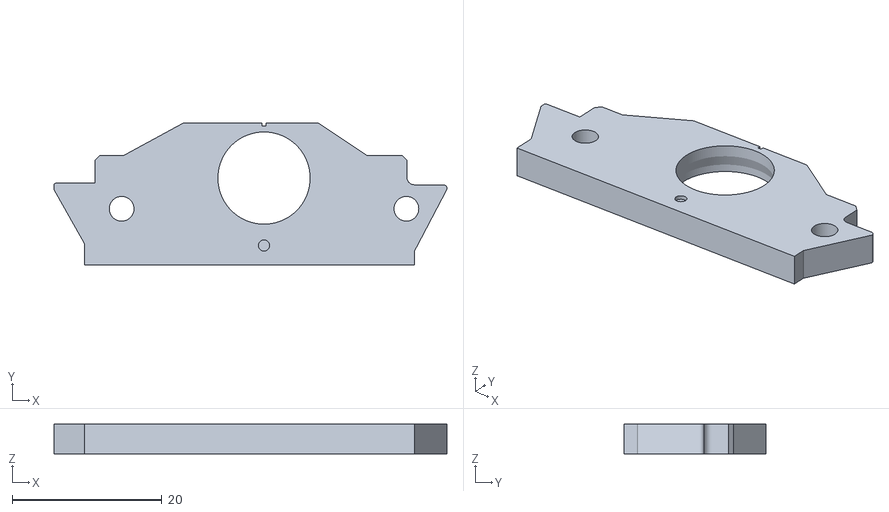
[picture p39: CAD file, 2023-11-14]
stl/hand-y-frontplate.stl
52.4 x 19.0 x 4.00

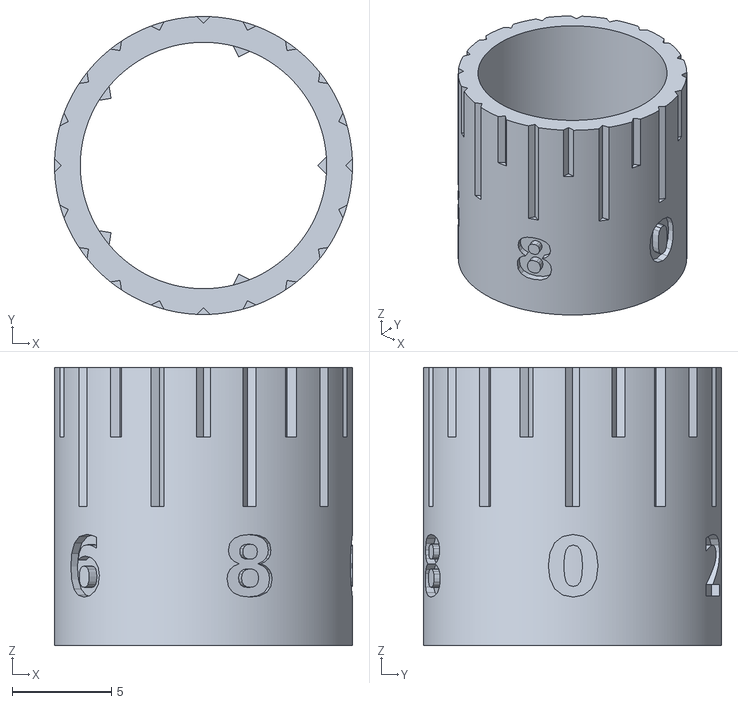
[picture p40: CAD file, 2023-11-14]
stl/hand-y-knob.stl
15.0 x 15.0 x 14.0

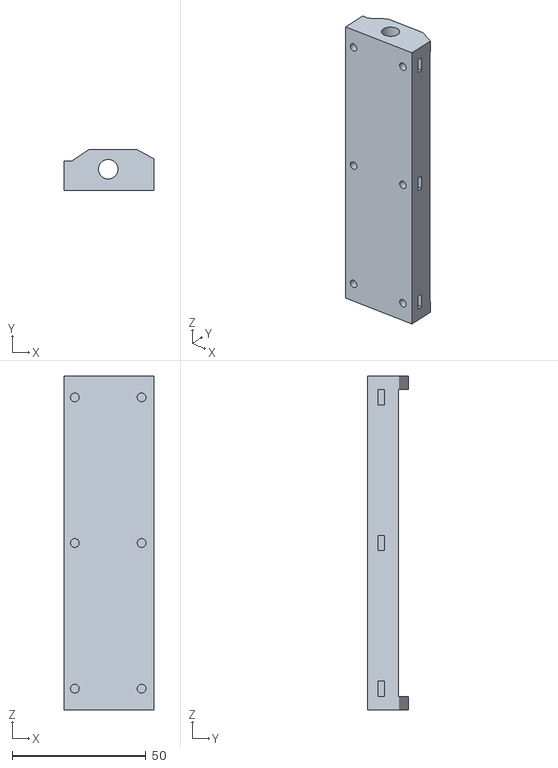
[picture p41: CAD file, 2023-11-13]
stl/all-y-channel.stl
33.6 x 15.4 x 125.0

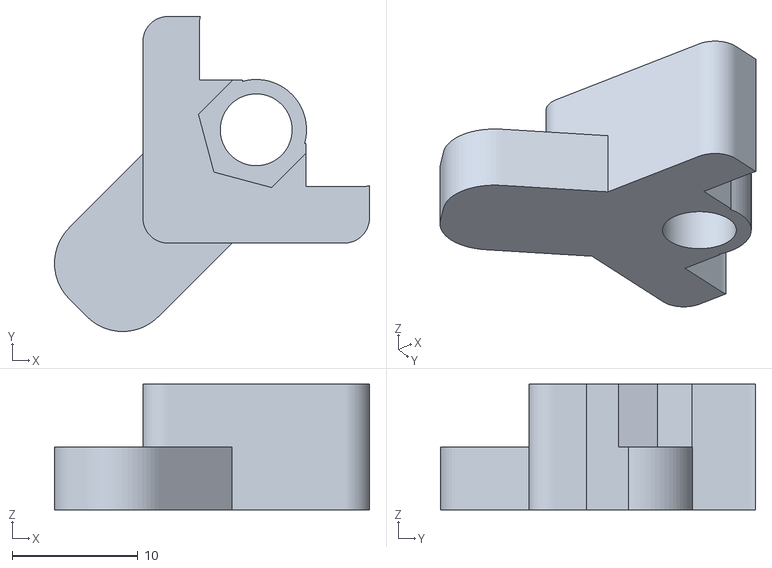
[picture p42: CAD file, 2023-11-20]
stl/cnc-stepper-nut-tool.stl
25.0 x 25.0 x 10.0

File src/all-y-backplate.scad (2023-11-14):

translate([0,0,0])
mirror([1,0,0]) outer();

module inner() {
    
    translate([0,0,0])
{
     difference() {
        union() {
        scale([1,1,25/3])
            mirror([1,0,0])
            translate([-17.0,-8,0])
                import("profile_inner.stl");
            
            translate([-1.3,5.9,0])
         cube_center([17.5,3,5]);
            
            intersection() {
            
          scale([0.98,0.96,21/3])
translate([21.4,-6.1,0])
rotate([0,0,180])
import("profile_outer.stl");
                
                translate([-1.3,5.9,0])
                cube_center([37.6,10,5]);
            }
            
        }
        
         
         for(i=[-12,12]) for(j=[5,20])
         translate([i,0,j])
         rotate([90,0,0])
         cylinder(d=2.5,h=100,center=true,$fn=64);
         
         translate([0,-.5,5])
         cube_center([14,12,50]);
         
         rotate([15,0,0])
         translate([0,5,6])
         cube_center([14,12,50]);
         
         translate([0,6,5])
         cube_center([18,12,50]);
         
         rotate([15,0,0])
         translate([0,6+5.5,5])
         cube_center([18,12,50]);
         
         translate([0,10.2-1.5,5])
         cube_center([100,10,100]);
    }
    
    
    difference() {
        cylinder(d=10.3,h=25,$fn=64);
        translate([0,0,-.1])
        cylinder(d=7.3,h=100,$fn=64);
        
         translate([0,-.5,5])
         cube_center([14,12,50]);
        
         translate([0,6,5])
         cube_center([18,12,50]);
    }
    
    
    
    
}

}

module outer() {
difference () {
    
            union() {
            difference() {
              
                scale([0.98,0.96,4/3])
                translate([21.4,-6.3,0])
                rotate([0,0,180])
                import("profile_outer.stl");
                
                
                for(i=[-1,1])
                translate([i*19.0,-4.1,0]) {
                cylinder(d=3.3,h=50,$fn=64);
              
                }
                
                
                translate([0,-9,3.5])
                cylinder(d1=1.5,d2=1.5,h=0.5,$fn=32);
                
                translate([-20.5,11.5,0])
                rotate([0,0,45])
                cube_center([20,10,50]);
                
                
                translate([17,11.5,0])
                rotate([0,0,-45])
                cube_center([20,10,50]);
            }
            //cube_center([58.4,58.4,4],r=4);
            translate([0,-.3,0])
            cylinder(d=14.7,h=4);
            
            for(i=[-1,1])
            translate([i*19.0,-4.1,0])
                cylinder(d=6,h=4,$fn=32);
            
            }


    translate([0,0,-.001]) {
    cylinder(d=12.3,h=50,$fn=128);
        cylinder(d=13.3,h=4-3,$fn=128);
        translate([0,0,4-3])
        cylinder(d1=13.3,d2=12.3,h=1.5,$fn=128);
    }
        
            
    for(i=[-1,1])
    translate([i*19.0,-4.1,0])
    cylinder(d=3.3,h=50,$fn=64);


    //cylinder(d=33,h=4,$fn=64);
}
}
//cylinder(d=7.8,h=4,$fn=64);

module cube_center(dims,r=0,$fn=64) {
    if(r==0) {
        translate([-dims[0]/2, -dims[1]/2, 0])
        cube(dims);
    } else {
        minkowski() {
            translate([-(dims[0]-2*r)/2, -(dims[1]-2*r)/2, 0])
            cube([dims[0]-2*r,dims[1]-2*r,dims[2]]);
            cylinder(r=r,$fn=$fn,h=0.0001);
        }
    }
}

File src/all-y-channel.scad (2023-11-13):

//translate([0,0,2])
mirror([1,0,0]) inner();
//mirror([1,0,0]) outer();

module inner() {
    
    translate([0,0,0])
{
     difference() {
        union() {
        scale([1,1,125/3])
            mirror([1,0,0])
            translate([-16.5,-8,0])
                import("profile_inner.stl");
            
            translate([-1.3,5.9,0])
         cube_center([17,3,5]);
            
            translate([-1.3,5.9,120])
         cube_center([17,3,5]); 
            
            intersection() {
            
          scale([0.98,0.96,125/3])
translate([21.4,-6.3,0])
rotate([0,0,180])
import("profile_outer.stl");
                
                translate([-2.3,5.9,0])
                cube_center([37.6,10,125]);
            }
            
        }
        
         
         for(i=[-1,1]) for(j=[8,125/2,125-8])
             scale([i,1,1])
         translate([12.5,0,j])
         rotate([-90,0,0]) {
             translate([0,0,-9])
            cylinder(d=3.3,h=10,$fn=64,center=true);
             
             
             translate([0,0,6])
            cylinder(d=3,h=10,$fn=64,center=true);
             
             translate([5.8/2,0,-4])
             cube_center([2*5.8,5.8,2.3]);
         }
         
         translate([0,-.5,5])
         cube_center([14,12,125-10]);
         
         
         translate([0,5,5])
         cube_center([18,12,125-10]);
         
         
         translate([-27.1,5,0])
         cube_center([20,50,125]);
         
         translate([0,10.2-1.5,5])
         cube_center([100,10,125-10]);
    }
    
    
    difference() {
        cylinder(d=11.8,h=125,$fn=64);
        translate([0,0,-.1])
        cylinder(d=7.3,h=150,$fn=64);
        
         translate([0,-.5,5])
         cube_center([14,12,125-10]);
        
         translate([0,6,5])
         cube_center([18,12,125-10]);
    }
    
    
    
    
}

}

module outer() {


difference() {
scale([0.98,0.96,2/3])
translate([21.4,-6.3,0])
rotate([0,0,180])
import("profile_outer.stl");
    
    /*
         for(i=[-10,10])
        translate([i,-2,0])
        cylinder(d=2.5,h=100,$fn=64);*/
    
    for(i=[-1,1])
translate([i*19.0,-4.1,0])
    cylinder(d=3.3,h=50,$fn=64);
    
    
    
translate([-20.5,11.5,0])
rotate([0,0,45])
cube_center([20,10,10]);
    
    
translate([17,11.5,0])
rotate([0,0,-45])
cube_center([20,10,10]);
    
    
}
difference() {
    translate([0,-1,0])
cylinder(d=15,h=2,$fn=64);
    translate([0,0,-.1])
    cylinder(d=12.3,h=50,$fn=64);
    translate([0,0,-.1])
cylinder(d=12.3,h=2,$fn=64);
}

for(i=[-1,1])
translate([i*19.0,-4.1,0])
difference()  {
    cylinder(d=6,h=2,$fn=32);
    translate([0,0,-.1])
    cylinder(d=3.3,h=50,$fn=64);
}


}
//cylinder(d=7.8,h=4,$fn=64);

module cube_center(dims,r=0,$fn=64) {
    if(r==0) {
        translate([-dims[0]/2, -dims[1]/2, 0])
        cube(dims);
    } else {
        minkowski() {
            translate([-(dims[0]-2*r)/2, -(dims[1]-2*r)/2, 0])
            cube([dims[0]-2*r,dims[1]-2*r,dims[2]]);
            cylinder(r=r,$fn=$fn,h=0.0001);
        }
    }
}

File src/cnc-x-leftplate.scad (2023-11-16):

module pentagon() {
    translate([0,-8.6-0.25,0])
    polygon(points=[[0,0],[-32.25,11],[-32.25,17.2],[32.25,17.2],[32.25,11]]);
}

difference() {
    union() {
        intersection() {
    
            cube_center([70,19.5*2+.5,6],r=1);
            union() {
    minkowski() {
        linear_extrude(height=15)
        pentagon();
        cylinder(d=2,h=0.001,$fn=16);
        rotate([0,0,45])
        cylinder(d=5,h=0.001,$fn=4);
    }
    
    
    translate([0,13,0])
    cube_center([70,13.5,15]);

    
}
    
        }
        
        for(i=[-1,1])
            translate([i*12.25,13.5,0])
            cube_center([5.8,6.8,14],r=0.5);
        
        
        
    }
    translate([0,0,6-1.75-1.5])
    cylinder(d=12.3,h=100,$fn=64);
    translate([0,0,6-1.75-1.5-2])
    cylinder(d1=13.3,d2=12.3,h=2,$fn=64);
    cylinder(d=13.3,h=6-1.75-1.5-2,$fn=64);
    
    translate([0,0,6-1.75])
    minkowski() {
        linear_extrude(height=2)
        pentagon();
        cylinder(d=0.5,h=0.001,$fn=16);
    }
    
    for(i=[-1,1]) {
            translate([-i*19,6.25,0])
        cylinder(d=3.3,h=100,$fn=32);
    }
    
    
    
    
        for(i=[-1,0,1]) { 
            translate([i*25,14.25,0])
            cube_center([12.5,5.8,100]);
        
        
            translate([i*25,14.25+3,0])
            cube_center([6.5,5,100]);
        }
    



}
    
    


module cube_center(dims,r=0,$fn=64) {
    if(r==0) {
        translate([-dims[0]/2, -dims[1]/2, 0])
        cube(dims);
    } else {
        minkowski() {
            translate([-(dims[0]-2*r)/2, -(dims[1]-2*r)/2, 0])
            cube([dims[0]-2*r,dims[1]-2*r,dims[2]]);
            cylinder(r=r,$fn=$fn,h=0.0001);
        }
    }
}

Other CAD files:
stl/all-y-backplate.stl
stl/cnc-z-nut-tool.stl
src/cnc-x-rightplate.scad
src/cnc-xy-cover.scad
src/cnc-y-frontplate.scad
src/cnc-z-nut-tool.scad
src/cnc-z-stop.scad
src/cnc-z-topplate-a.scad
src/cnc-z-topplate-b.scad
src/hand-y-frontplate.scad
src/hand-y-knob.scad

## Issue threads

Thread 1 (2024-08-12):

Missing enclosure instructions and part-list

wonder76, 2024-08-12:
That would be great to have build instructions for the enclosure and a part-list too...

dheera, 2024-08-13:
Hi,
It's based on 20cm aluminum extrusions which I cut with a miter saw, tapped, and put together with off-the-shelf fasteners. 8020 Inc sells these ("2020 series") but there are also a lot of much cheaper China-made extrusions you can get which are just fine and save a lot of money, just that the fasteners are not always cross-compatible with the 8020 stuff so make sure you get the right fasteners for those.

The panels are polycarbonate ("lexan") which I got custom cut at TAP Plastics if you're in the bay area. Do NOT use acrylic, it can shatter and crack easily if a high speed projectile like a milling bit hits it.

wonder76, 2024-08-13:
thx a lot!

Closed 2024-08-13.

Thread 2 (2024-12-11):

Not an issue but revision

sanscorp1, 2024-12-11:
I would like to comment on some things but do not want to fork the whole project.
The only option I see now is to create an issue.

I started on this project (in PLA, sorry!) because I like the extention of the Y and Z axis.
The X axis is left untouched because I allready had a (aluminum) CNC kit and NEMA17 steppers.

I printed all the parts in ABS but the larger pieces kept warping.
Glass bed with proper 3DLAC adhesive, brim of 20mm wide, enclosure, bed 110 nozzle 250 and still crappy..
Even all the snug fits were very loose while the PLA work and fit perfectly!
I could have tried PETG which works a lot better then ABS but the only fluorecent yellow I had was PLA.
It is strong enough, just not very chemical or heat resistant.

First of all you do not have to drill to 3mm to be able to install longer M3 screws into the bed.
As long as you do not try to install 30mm of length into the bed it will be just fine.
This takes away a lot of work and possible breaking the (extra long) drill bits.
The slots are open and will expand enough to accept the M3 bolts.

Perhaps a feature request but integrating endstops into the design might be worth it.
Is there any way this could be implemented?

For the NEMA 17 conversion I only printed this: https://www.thingiverse.com/thing:526443/files
The adapter plate allows you to convert easily without losing strength.

I am also looking at removing the stock wheel on each leadscrew to gain a little bit of extra space.
A (printable) flexible motor mount is all you need, I took an 5mm to 8mm coupler because I had laying them arround and printed a 4.5x8x4mm spacer to fit the thin leadscrew into the coupler.
Still have to figure out the rest for now.

Allthough stacking spacers is not the ideal solution, the bearings take up a lot of room, so extending the leadscrews by removing the handwheel might be a good solution to get things stronger and more secure, also making the use of locktite in the leadscrew nuts not needed. The bed is smooth enough to operate so steppermotors will have no issue moving them. The backlash is also very good solvable by adjusting the grub screws and leadscrew nut properly.

Bonus tip that really helped me with my enclosure for the 3D printer and the acrylic panels collecting dust:
Use a splash of laundry softner + water (10/90%), apply to a cloth and wipe the acrylic clean.

dheera, 2024-12-30:
Hi! Thanks for writing! Some comments:
- You're correct that you can just install regular M3 screws, but I preferred to go all the way through and screw it down from both sides for it to be more secure. Because the channel is "half open" I don't trust self-tapping screws to hold inside it
- PLA is not chemically resistant, as you noted. I am especially not confident it can withstand machining oil, cleaning sprays, corrosive metal shavings, and other things commonly used on the mill
- I agree removing the handwheel would be the "cleanest" solution if you can, so that there is enough length for the bearings and locknuts to work. I left them in because the AliExpress couplers are super easy to install.
- You mentioned "acrylic" -- I recommend switching to polycarbonate if you can. If there is a flying metal part inside, acrylic can shatter and crack, while polycarbonate will tend to absorb the shattered part instead. Safety goggles are usually made from polycarbonate.

mmalecki, 2025-02-10:
Just got the Proxxon MF70 and looking to do this conversion, thought I'd chime in with something I found while researching, as I wasn't fully ready to do the long drilling bit either, since my hand is ridiculously unsteady holding a power drill. On a tutorial for removing backlash, a person on the [Ships of scale forum tapped the holes for M3 instead](https://shipsofscale.com/sosforums/threads/upgrading-the-proxxon-micro-compound-table-kt-70.12516/). The opening should be perfect for that, and if you then need to do the threaded rods approach still, I can envision taking a long 3.2 mm drill to nullify that thread.

dheera, 2025-05-27:
Hi @mmalecki

You could tap them for M3 but I wouldn't trust that half-open channel with a screw thread. I think some of those steppers could theoretically rip the screws right out of the channel without a full circle of thread.
